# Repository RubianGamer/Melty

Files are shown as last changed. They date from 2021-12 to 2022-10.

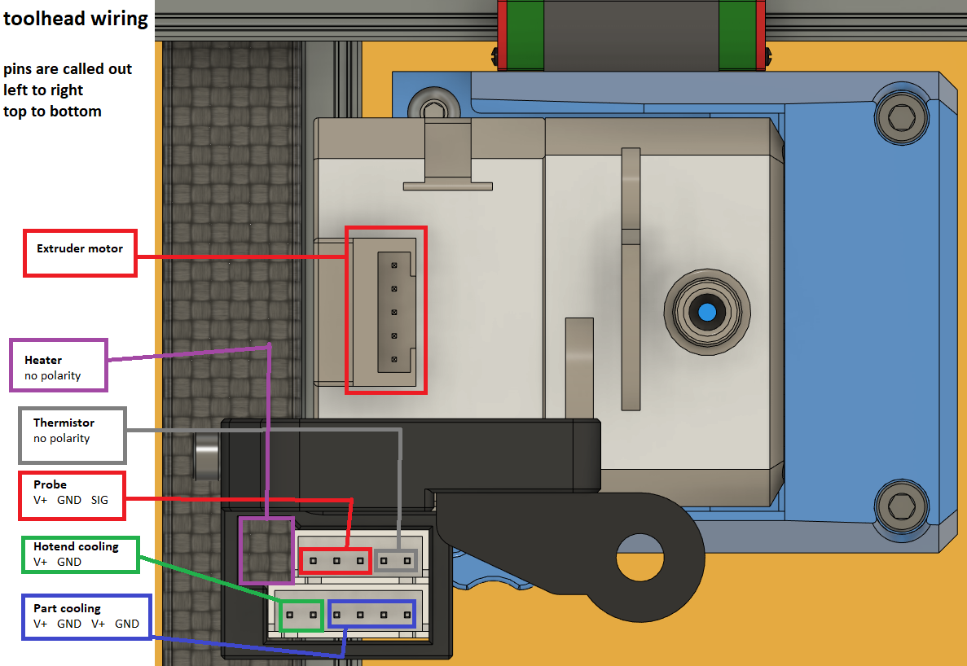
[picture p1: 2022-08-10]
beta releases/beta 3/wiring schematics/toolhead_wiring.png

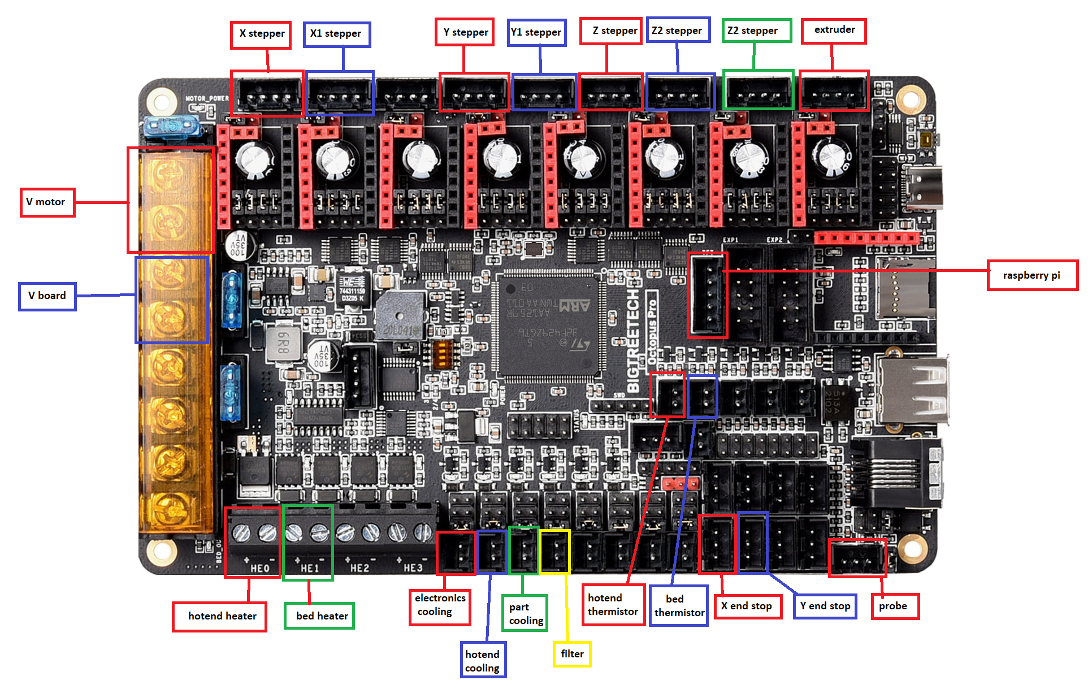
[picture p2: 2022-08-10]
beta releases/beta 3/wiring schematics/octopus wiring.png

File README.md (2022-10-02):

# Melty
 A medium to large scale, scalable crossed gantry FDM 3D printer 

# featurelist

- crossed gantry/crossXY kinematics
- fully enclosed printing chamber with air filtration
- scalable print volume of 250x250x300 to 500x500x500mm
- 3 point auto bed leveling
- options for leadscrew or belted Z
- 24v printer and 48v XY motion using 5160HV drives and BTT octopus pro
- mains powered bed
- rigid 3030 and 3060 frame extrusions
- shortest possible 12mm 2MGT belts for motion
- MGN12H rails for stationary rails, MGN9C for moving rails backed by MakerBeamXL or a carbon fiber tube
- phaetus rapido (UHF) and dragon UHF supported direct drive toolhead using a bondtech LGX (lite)
- easily accesable rear mounted electronics
- internal spool holder to reduce printer footprint and keep filament dry on long prints (external avalible for larger format spools)
- filtered air circulator to reduce smell and toxic fumes

# Discord

if you want more info on this printer, or need help with other 3d printing/printer related things, feel free to joing the discord
https://discord.gg/2XBTuWrQu5

# patreon

if you want to support my work, feel free to join my patreon
https://www.patreon.com/RubianGamer

# Renders

render_front

render_rear

render_top

irl

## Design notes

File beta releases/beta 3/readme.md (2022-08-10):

# changelog from beta 2

- added option for belted Z
- updated leadscrew driven Z for some extra Z height
- added 1515 CF tube for the gantry (not final)
- updated electronics enclosure
- added support for LGX lite extruder
- swapped to molex microfit connectors
- added support for long shaft steppers on XY
- refined motion system to handle high accel better
- magnetic panels now use larger magnets
- external spool holder for larger spool sizes
- changed nozzle brush location
- updated toolhead body for better hotend cooling
- tweaked bed frame extrusion lenghts
- better enclosed electronics
- bunch of smaller optimiziations

# planned features

- support for dragon UHF and rapido UHF
- rigid mounted side/back/bottom panels
- rubber grommets in rear panel for cable passthough (removing the connectors, they can be annoying at times)
- potentially custom extruder using bondtech BMG internals
- improved mount for XY steppers with normal sized shafts using couplers
- hinged door (yes some day this will be added :)

# removed

support for original dragon, it doesnt have enough flow to keep up (files might still be made avalible in the future)

# notes

the BOM might not be fully up to date, as stuff has been changing a lot recently and i lost track on all the changes in the BOM. it will still be a great indicator of the stuff you need for a price estimate.

render_front

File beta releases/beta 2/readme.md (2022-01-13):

changelog from beta 1:
- added a BOM that should be accurate
- added printed parts. not fully up to date, but has all the needed mechanical parts
- added sample config (untested, use with caution)
- added filtered air circulator
- added nozzle brush and purge bucket
- fixed the bed position
- added passtrough for the Z steppers
- added passthough for the reverse bowden tube
- added nameplate
- added carbon fiber gantry option
- added toolhead for rapido hotend

changes planned for next update:
- change carbon fiber gantry to 1515 tubes
- add hinging option for top and front panel
- fix T nut interferance on the makerbeam gantry
- higher part cooling fan duct
- led strips

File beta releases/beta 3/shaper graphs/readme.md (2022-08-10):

these graphs are from a 250 build with a LGX lite, leadscrew driven Z and a aluminum gantry

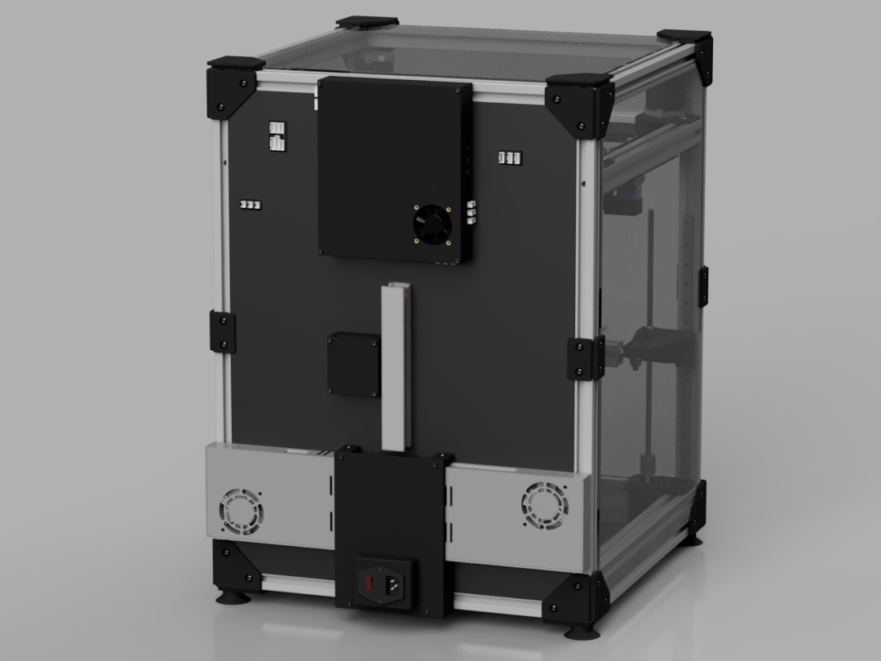
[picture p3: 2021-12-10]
beta releases/beta 1/renders/melty_electronics.png

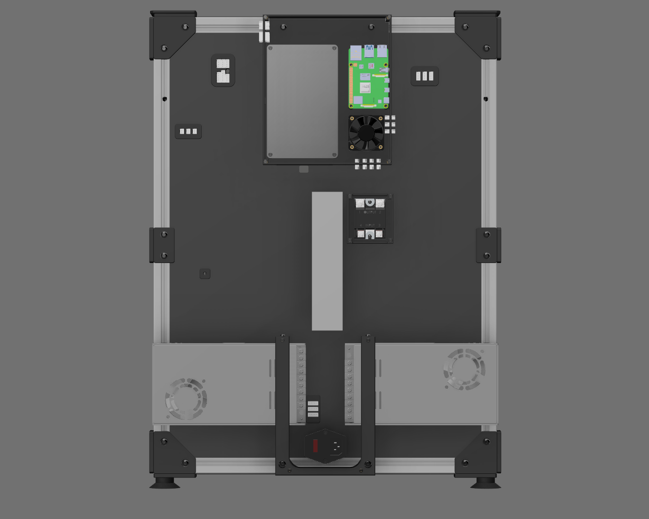
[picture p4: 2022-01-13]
beta releases/beta 2/renders/melty-electronics.png

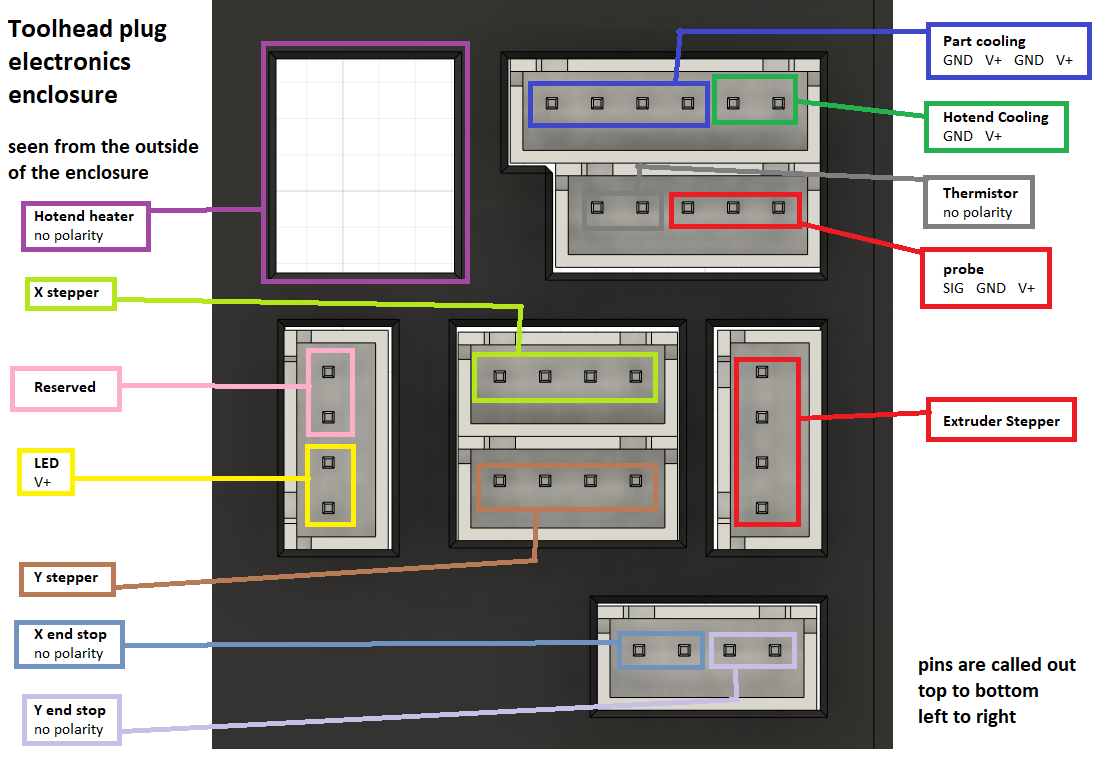
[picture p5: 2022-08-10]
beta releases/beta 3/wiring schematics/Toolhead_plug_electronics_enclosure.png

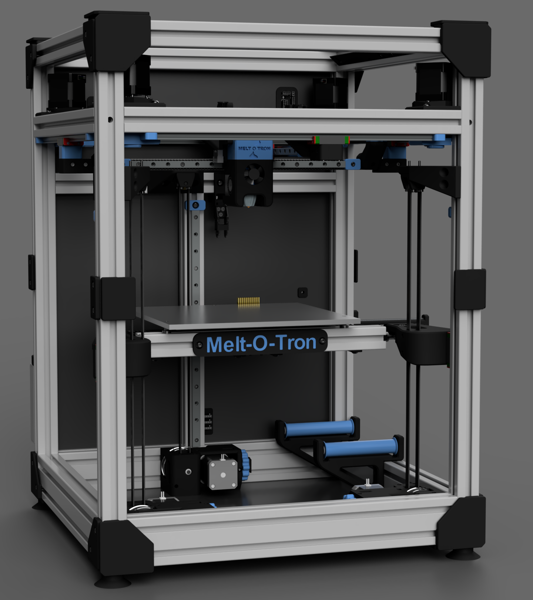
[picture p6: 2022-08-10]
beta releases/beta 3/renders/melty.png

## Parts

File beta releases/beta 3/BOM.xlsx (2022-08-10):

this part of the BOM is for the base build. You will need all of these things for every build.
some of these parts get repeated in the specific BOM for your configuration. You need to add the stuff listed under that section to this for the total quantity needed. Screws have been counted for all the possible layouts. i still recommend getting a surplus of screws for future upgrades and counting mistakes.
category | part name | quantity | obtained | source | alt source | notes
hardware | M2.5x6 BHCS | 4 |  | schrauben-expert (https://schrauben-expert.de/) | McMaster-carr (https://www.mcmaster.com/screws/) | these might be included with your hotend of choice
hardware | M2.5x8 BHCS | 4
hardware | M3x6 BHCS | 51 |  |  |  | These are exact ammounts, its recommended to get some extra
hardware | M3x8 FHCS | 15
hardware | M3x8 SHCS | 169
hardware | M3x12 BHCS | 16
hardware | M3x14 SHCS | 8
hardware | M3x20 SHCS | 27
hardware | M3x35 SHCS | 8
hardware | M5x10 BHCS | 68
hardware | M5x12 BHCS | 55
hardware | M5x25 BHCS | 4
hardware | M8x10 BHCS | 35
hardware | M8x30 BHCS | 3
hardware | M3 hex nut | 8 |  | schrauben-expert (https://schrauben-expert.de/DIN-439-Hexagon-Nut-flat-steel-plated)
hardware | M4 knurled nut | 3 |  | aliexpress (https://www.aliexpress.com/item/1005003385966630.html) |  | get them from stainless steel for better heat isolation of the bed
hardware | M3 locknut | 8 |  | aliexpress
hardware | M8 locknut | 3
hardware | M3 T-nut | 45 |  | aliexpress (https://www.aliexpress.com/item/32818082697.html) |  | roll in ones are rare, but if you can find them they will be easier to work with.
hardware | M5 T-nut | 123 |  | aliexpress (https://www.aliexpress.com/item/33023772052.html)
hardware | M3 heatset insert | 78 |  | aliexpress (https://www.aliexpress.com/item/1005002530005649.html) |  | specific size needs to be M3x5x4
hardware | 5x10x1 shim | 16 |  | schrauben-expert (https://schrauben-expert.de/DIN-125-Washer-without-bevel-A-Stainless-Steel) |  | make sure these are shims and not washers. Washers have variying heights, shims are more precise.
hardware | 6x3 magnet | 32 |  | aliexpress (https://www.aliexpress.com/item/1005001614008679.html)
hardware | 120-130mm M5 steel rod | 2 |  | aliexpress (https://www.aliexpress.com/item/1005003609354901.html) |  | used for the spool holder, if you are going with a different spool holder, you don’t need these
hardware | rubber compressor feet | 4 |  | aliexpress (https://www.aliexpress.com/item/32990144547.html) |  | if you don’t like these, any feet with a M5 hole in the bottom should work
hardware | M8 rodend | 3 |  | aliexpress (https://www.aliexpress.com/item/32741967134.html)
electronics | LRS-200-24 | 1 |  | digikey (https://www.digikey.nl/en/products/detail/LRS-200-24/1866-3332-ND/7705026?itemSeq=385607687) |  | DO NOT cheap out on the power supply, get them from a known good brand 48v is only needed if you go with 48v XY motion
electronics | LRS-200-48 | 1 |  | digikey (https://www.digikey.nl/en/products/detail/LRS-200-48/1866-3336-ND/7705025?itemSeq=385607640)
electronics | BTT octopus (pro, F446) | 1 |  | aliexpress (https://www.aliexpress.com/item/1005003349906490.html) |  | both the regular and pro will work, but you will need the pro for 48v XY motion. Non pro also needs a additional BAT85 diode as the build in probe port does not work correctly with the type of probe used
electronics | TMC2209 drivers | 4 |  | aliexpress (https://www.aliexpress.com/item/4000249242465.html) |  | you will need 4 additional drivers if you are not going with 48v XY motion
electronics | TMC5160HV drivers | 4 |  | watterott (https://shop.watterott.com/SilentStepStick-TMC5160-Stepper-motor-driver) |  | only needed when going for 48v XY motion. Make sure you get the high voltage ones, since the regular ones can only do 36v
electronics | raspberry PI 4 | 1 |  | find local source |  | PI 3B+ works as well.
electronics | wago 221-415 | 3 |  | digikey (https://www.digikey.nl/en/products/detail/221-415%2fK194-4045/2946-221-415%2fK194-4045-ND/13549349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) |  | other types of wire nuts might work as well.
electronics | fused power inlet | 1 |  | aliexpress (https://www.aliexpress.com/item/32959398453.html) |  | this one comes with a 10A fuse. I recommend replacing the fuse for something closer to the max power draw of your printer (5A for a 250 build)
electronics | JST-XH 2 pin female | 6 |  | aliexpress |  | buy one of each of the kits, they have enough for the entire build
electronics | JST-XH 3 pin female | 1
electronics | JST-XH 4 pin female | 9
electronics | JST-XH pins | 60
electronics | JST-PH 4 pin female | 8
electronics | JST-PH pins | 32
electronics | 1x2 molex male/female | 6 |  | aliexpress |  | kits come with both male and female side, and also include the needed pins for the 2x7, both links are needed as male and female plugs are sold seperately
electronics | 1x4 molex male/female | 18
electronics | 2x7 molex male/female | 3 |  | aliexpress (https://www.aliexpress.com/item/4000969264416.html) | aliexpress (https://www.aliexpress.com/item/32878728191.html)
electronics | molex pins | 150 |  | included in kits
electronics | ferrule connectors | 4 |  | aliexpress (https://www.aliexpress.com/item/33040940850.html)
electronics | thermal fuse | 1 |  | aliexpress (https://nl.aliexpress.com/item/32995866765.html) |  | get one with the max temp you are planning on using the bed at. Not recommended going above 150c, as this is the long term usage spec of the glue used on the heater
electronics | spade connectors | 20 |  | lektor (https://lecktor.com/en/connectors/291-flanged-spade-terminals-yf2-4k.html) | aliexpress (https://www.aliexpress.com/item/4000105363591.html) | make sure to get the right size for the wires you are using.
electronics | AWG16 cable | 10 meters |  | lektor (https://lecktor.com/en/cables/644-336-heluflon-fep-6y-16awg-15mm2.html) |  | motion rating is not stricly needed, but is recommended. Recommended to get 3 different colors
electronics | AWG20 cable | 10 meters |  | lektor (https://lecktor.com/en/cables/645-340-heluflon-fep-6y-20awg-05mm2.html) |  | make sure these are rated for use in drag chains. If 24AWG is out of stock, you can replace it with 20AWG.
electronics | AWG24 cable | 50 meters |  | lektor (https://lecktor.com/en/cables/646-344-heluflon-fep-6y-24awg-025mm2.html)
electronics | 3010 axial fan | 1 |  | aliexpress (https://www.aliexpress.com/item/4000608874732.html) |  | DO NOT get fans with low air flow and static pressure, you will have heat creep issues
electronics | 5010 axial fan | 1 |  | aliexpress (https://www.aliexpress.com/item/4000609105669.html) |  | get something quiet, you don’t need much cooling for the electronics.
electronics | 110-220v 20A SSR | 1 |  | ratrig (https://www.ratrig.com/hardware2/electronics/clin-ssr-40a-relay.html) |  | DO NOT cheap out and get a cheap chinese one, get one from a known good brand. Get the highest amp rated you can (within reason)
electronics | 10x11 drag chains | 2 |  | aliexpress (https://www.aliexpress.com/item/33000014666.html) |  | if you have some laying around, but don’t have end pieces, you can print these.
electronics | cable raceway | 1 |  | prited |  | easy to print, so no need to buy them seperately
motion | LDO-42STH48-2504AH(S55) or LDO-42STH48-2004MAH(ANX)(S80) | 4 |  | lukeslabonline (https://lukeslabonline.com/collections/ldo/products/longboi-ldo-nema-17-motor-high-temp-ldo-42sth48-2504ahs55) | caribou3d (https://caribou3d.com/en/annex-k3/897-09-stepper-motor-set-ldo-42sth48-2004mahanxs80.html) | these are steppers with long shafts. Normal steppers don’t have long enough shafts to work correctly. Any nema17 stepper with a shaft of at least 55mm long should work the LDO-42STH48-2504AH(S55) is great for printing at high speed, but has some issues with VFA at low printing speeds and is currently only avalible from one vendor in the USA. the LDO-42STH48-2004MAH(ANX)(S80) is a great 0.9 deg alternative, but you need to shorten the shafts a bit to not have them stick out, but have a lower top speed.
motion | 12mm 20 tooth GT2 pulley | 4 |  | aliexpress (https://www.aliexpress.com/item/33023279793.html) |  | you can swap to a 24 tooth pulley to get some more speed, but loose some acceleration. For realistic printing this doesn’t matter.
motion | 12mm GT2 belts | 5 meters |  | aliexpress (https://www.aliexpress.com/item/32952396111.html) |  | gates belts are recommended
motion | F695 bearing | 10 |  | aliexpress (https://www.aliexpress.com/item/757340601.html) |  | both ZZ and RS bearings work
motion | 695 bearing | 10 |  | aliexpress (https://www.aliexpress.com/item/558040550.html)
motion | MGN12H 350mm linear rail | 7 |  | robodigg (https://www.robotdigg.com/product/766/Quality-440C-SUS-MGN12-linear-rail-with-carriage) |  | cheap china rails will work, but its not recommended
motion | MGN9C linear rail | 2 |  | robodigg (https://www.robotdigg.com/product/779/Quality-440C-SUS-MGN9-linear-rail-with-carriage)
motion | ball bearing grease | 1 |  | source locally |  | any grease made for ball bearings should work. Don’t use oil as it doesn’t last as long
panels | top panel (440x440mm) | 1 |  | source locally |  | ideally from something transparent. Polycarbonate is recommended.
panels | side panels (600x440mm) | 3
panels | bottom panel (440x440mm) | 1 |  |  |  | ideally solid color. ACM/dibond are recommended and is easy to work with.
panels | back panel (600x440mm) | 1
buildplate | aluminum build plate | 1 |  | lektor (https://lecktor.com/en/vtd-buildplate/649-universal-250x250mm-build-plate.html) |  | make sure its cast so it doesn’t warp after repeated heating cycles. Hole mounting is the same as on the voron trident bed, so you can buy those if you have issues sourcing a bare plate.
buildplate | magnet sheet | 1 |  | lektor (https://lecktor.com/en/v2x-buildplate/481-magnetic-foil-260x260x1mm.html) |  | make sure to get a oversized magnet to make applying it easier.
buildplate | silicone heater | 1 |  | keenovo (https://keenovo.store/collections/standard-keenovo-silicone-heaters/products/keenovo-square-silicone-heater-3d-printer-build-plate-heatbed-heating-pad) |  | DO NOT get a cheap chinese heater, get a genuine one from keenovo. Recommended to have it be slightly undersized by 40mm, but some vendors might have a full cover heaters with holes cut out for the mounting.
buildplate | flexplate | 1 |  | aliexpress (https://nl.aliexpress.com/item/1005004182077447.html)
buildplate | nozzle brush | 1 |  | source locally
frame | 3030 B-Type 645mm | 4 |  | aluxprofiel | ratrig | ends do not need to be tapped
frame | 3030 B-Type 425mm (tapped) | 9 |  |  |  | both ends need to be tapped with M8 at least 10mm deep.
frame | 3030 B-Type 375mm (tapped) | 1
frame | 3030 B-Type 330mm (tapped) | 1
frame | 3030 B-Type 215mm (tapped) | 1
frame | 3060 B type 425mm (tapped) | 4
toolhead | rapido or dragon UHF | 1 |  | aliexpress (https://www.aliexpress.com/item/1005003954881267.html) | 3djake (https://www.3djake.com/phaetus/dragon-hotend-uhf) | pick whichever you like the most. rapido HF can struggle to keep up, so the UHF version is reccomended
toolhead | LGX or LGX lite | 1 |  | lektor (https://lecktor.com/en/24-extruders) |  | LGX is prefered for non speed printing, LGX lite is better for speed printing, but has lower torque output, so might struggle to keep up
toolhead | 4mm OD 3mm ID PTFE tube | 2 meters |  | aliexpress (https://www.aliexpress.com/item/1005003593762891.html) |  | get clear PTFE tube, it makes it easier to see where your filament is when loading.
toolhead | 4mm OD 1.9mm ID PTFE tube | 20cm |  | aliexpress (https://nl.aliexpress.com/item/1005001370675514.html) |  | can be anything you have laying around. Doesn’t come into contact with anything hot, so doesn’t need to be fancy tubing.
toolhead | 4010 blower | 2 |  | aliexpress (https://www.aliexpress.com/item/32798634077.html) | digikey (https://www.digikey.com/en/products/detail/delta-electronics/BFB0412HHA-A117/5022816) | delta is recommended, but might be hard to find outside of the US
toolhead | omron TL-Q5MC2 | 1 |  | lektor (https://lecktor.com/en/sensors/557-proximity-sensor-tl-q5mc2-2m-4536854114885.html) | aliexpress (https://www.aliexpress.com/item/32849513527.html?) | lektor has genuine omron switches. The aliexpress ones linked worked fine for me.
filament | ABS primary color | 2kg |  | 3djake | 3djake | 3djake niceABS is rebranded titanX, and prints very easily on non enclosed printers. Filamentum can also be printed without enclosure, but might encounter some warping on larger parts you can also print the parts out of PC for increased thermal resistance.
filament | ABS secundary color | 500g
filter | 5015 blower | 2 |  | aliexpress (https://www.aliexpress.com/item/1005003652882829.html) |  | get cheap fans with ball bearings, they will be used in a really hot enviroment so wont have the longest lifetime. Recommended to get some spares
filter | activated carbon | 1 liter |  | source locally |  | DO NOT get acid washed carbon, this can cause your printer to rust really fast. You want to get (virgin) coconut shell based carbon that is steam activated
aluminum gantry
gantry | 1515 (makerbeam XL) extrusion 470mm | 2 |  | makerbeam (https://www.makerbeam.com/makerbeamxl/makerbeamxl-15x15mm-profile-lengths-anodised-in-bl/) |  | other types of 1515 extrusions will work as well, just make sure to get the right T-nuts for them. Ends don’t need to be tapped
gantry | M3 makerbeam XL T-nut | 38 |  | makerbeam (https://www.makerbeam.com/t-slot-nuts-for-makerbeamxl-50p.html) |  | you can also use M3 hex nuts with printed traps.
carbon fiber gantry
gantry | 15x15x13 cf tube 470mm long | 2 |  | source locally | contact mellow | mellow makes custom carbon fiber tubes at a little cost. All the files needed for it are in the repo. If you can get them from mellow, it is highly recommended as cutting/drilling carbon fiber can be a pain to do correctly.
gantry | M3 washer | 10 |  | schrauben-expert (https://schrauben-expert.de/DIN-9021-Washer-large-Stainless-Steel)
gantry | M3 locknut | 10 |  | aliexpress (https://www.aliexpress.com/item/32798773566.html) |  | can be normal hex nuts, but nylock nuts are recommended since you cant torque them a lot without crushing the carbon fiber tube.
gantry | M3 heatset insert | 28 |  | aliexpress (https://www.aliexpress.com/item/1005002530005649.html)
leadscrew driven Z
recommended for larger build volumes
Z axis | 335-370mm leadscrew | 3 |  | aliexpress (https://www.aliexpress.com/item/32792571155.html) |  | recommended is 2mm pitch, 8mm lead, but finer will work as well. Finer leadscrews are recommeded for larger build volumes to aid in keeping the bed up on power down make sure you match the leadscrew nut lead/pitch to the leadscrews you are getting
Z axis | leadscrew nut | 3 |  | aliexpress (https://www.aliexpress.com/item/32696626893.html)
Z axis | flexible coupler | 3 |  | aliexpress (https://www.aliexpress.com/item/4000811647280.html) | aliexpress (https://www.aliexpress.com/item/32862693235.html) | alternate source is a different type of flexible coupler. Supposed to work better then other types of flexible couplers, but not personally tested it.
Z axis | 40mm stepper motor | 3 |  | ratrig (https://www.ratrig.com/hardware2/electronics/nema-17-stepper-motor.html) |  | max supported length is 48mm, but 40mm should be plenty
Z axis | 5mm ball bearing | 3 |  | aliexpress (https://www.aliexpress.com/item/1005003281616396.html) |  | used to support the couper so it doesn’t compress under the weight of the bed, but still allowing the coupler to flex.
Z axis | M3 locknut | 12 |  | aliexpress (https://www.aliexpress.com/item/32798773566.html)
belt driven Z
not recommended for larger build volumes as you might run into issues with the bed falling down when the motors get powered down
Z axis | 60mm stepper motor | 3 |  | OMC-stepperonline (https://www.omc-stepperonline.com/3-pcs-nema-17-bipolar-1-8deg-65ncm-92oz-in-2-1a-3-36v-42x42x60mm-4-wires-3-17hs24-2104s) |  | larger stepper motors are recommended over smaller ones for the increased detent torque
Z axis | GT2 80T 9/10mm pulley | 3 |  | aliexpress (https://nl.aliexpress.com/item/32997318588.html) |  | if you want to save some money, you should be able to print these as well, models can be found online.
Z axis | GT2 20T 9/10mm pulley | 3 |  | aliexpress (https://nl.aliexpress.com/item/32995102911.html) |  | can be replaced with 16T pulleys.
Z axis | GT2 16T 9/10mm pulley | 3 |  | aliexpress (https://nl.aliexpress.com/item/32995138803.html)
Z axis | GT2 20T 9/10mm idler | 3 |  | aliexpress (https://nl.aliexpress.com/item/32750484488.html) |  | can be both smooth and toothed.
Z axis | 9/10mm 202-GT2 closed loop belt | 3 |  | aliexpress (https://nl.aliexpress.com/item/4000034021834.html) |  | belt length needs to be 202mm
Z axis | 2GT 9/10mm open loop belt | 3 meters |  | aliexpress (https://nl.aliexpress.com/item/32608096392.html)
Z axis | 695 bearing | 9 |  | aliexpress (https://www.aliexpress.com/item/558040550.html) |  | both ZZ and RS bearings will work
Z axis | M3 heatset insert | 21 |  | aliexpress (https://www.aliexpress.com/item/1005002530005649.html)
Z axis | M3 locknut | 6 |  | aliexpress (https://www.aliexpress.com/item/32798773566.html) |  | normal M3 hex nuts will work as well, but you might loose belt tension over time due to vibrations
Z axis | M5x60 D cut shaft | 3 |  | aliexpress (https://nl.aliexpress.com/item/4000303705414.html) |  | make sure it’s a D shaft
Z axis | M5x25 shaft | 3 |  | aliexpress (https://www.aliexpress.com/item/4000473863693.html) |  | make sure it’s a round shaft, D shafts can cause damage to the bearings inside the idlers

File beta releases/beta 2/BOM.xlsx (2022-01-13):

category | part name | quantity | obtained | source | notes
hardware | M2.5x6 SHCS | 4 |  | schrauben-expert (https://schrauben-expert.de/) | get whichever type of material you want. Numbers given are higher then actually used to account for counting errors. Exact ammounts are given for M5x25 and M8x30 M3x6SHCS only needed for carbon fiber gantry M2,5x8 SHCS should be included with your hotend of choice
hardware | M2.5x8 SHCS | 4
hardware | M3x6 BHCS | 25
hardware | M3x6 SHCS | 10
hardware | M3x8 FHCS | 15
hardware | M3x8 SHCS | 150
hardware | M3x12 BHCS | 2
hardware | M3X12 SHCS | 25
hardware | M3x14 SHCS | 15
hardware | M3x20 SHCS | 50
hardware | M3x35 SHCS | 20
hardware | M4x14 BHCS | 6
hardware | M5X10 BHCS | 90
hardware | M5x12 BHCS | 30
hardware | M5X25 BHCS | 5
hardware | M8x10 BHCS | 40
hardware | M8x30 BHCS | 3
hardware | M3 nut | 10
hardware | M4 knurled nut | 3 |  | aliexpress (https://www.aliexpress.com/item/1005003385966630.html)
hardware | M3 locknut | 25 |  | aliexpress (https://www.aliexpress.com/item/32798773566.html)
hardware | M8 locknut | 5
hardware | M3 T nut | 65 |  | aliexpress (https://www.aliexpress.com/item/32818082697.html) | can be any type, but roll in nuts are prefered, since you can insert them after building the frame. Needs to be compatible with 3030 B type extrusions. Links have both M3 and M5 as options
hardware | M5 T nut | 150 |  | rat rig (https://www.ratrig.com/aluminium-profiles/t-slot-30-b-type/accessories-30-series/nuts/t-nut-square-3030-1-unit.html)
hardware | makerbeamXL M3 nut | 50 |  | makerbeam (https://www.makerbeam.com/t-slot-nuts-for-makerbeamxl-50p.html) | not needed if you are going with a carbon fiber gantry.
hardware | M3 heatset insert | 85 |  | lektor (https://lecktor.com/en/nuts/506-230-threaded-insert-m3x5x4.html) | get the M3 x D5.0 x L4.0 variant
hardware | M3x0.5 washer | 10 |  | schrauben-expert (https://schrauben-expert.de/DIN-125-Washer-without-bevel-A-32x7x05-Steel-zinc-plated) | only needed when using the carbon fiber gantries, alternatively, you can get the larger ones for more even weight distribution https://schrauben-expert.de/DIN-9021-Washer-large-32x9x08-Steel-zinc-plated
hardware | 5x10x1 shim | 20 |  | schrauben-expert (https://schrauben-expert.de/DIN-125-Washer-without-bevel-A-53x10x10-Brass) | material can also be stainless steel
hardware | 5mm ball bearing | 3 |  | aliexpress (https://www.aliexpress.com/item/1005003281616396.html) | used to take the load off of the flexible couplings while still allowing them to flex
hardware | 6x3 neodynium magnet | 60 |  | alexpress (https://www.aliexpress.com/item/1005001614008679.html) | other types of magnets of the same size might work as well, but will be less strong
hardware | 120-125mm M5 steel rod | 2 |  | aliexpress (https://www.aliexpress.com/item/1005003609354901.html) | used for the spool holder. If you are using a different spool holder you can ignore these
hardware | rubber compressor feet | 4 |  | aliexpress (https://www.aliexpress.com/item/32990144547.html)
hardware | M8 rodend | 3 |  | aliexpress (https://www.aliexpress.com/item/32741967134.html)
electroncis | LRS-200-24 | 1 |  | digikey (https://www.digikey.nl/en/products/detail/LRS-200-24/1866-3332-ND/7705026?itemSeq=385607687) | DO NOT cheap out on the power supply
electroncis | LRS-200-48 | 1 |  | digikey (https://www.digikey.nl/en/products/detail/LRS-200-48/1866-3336-ND/7705025?itemSeq=385607640) | only needed if you are running 48V for XY motion, DO NOT cheap out
electroncis | BTT octopus PRO | 1 |  | aliexpress (https://www.aliexpress.com/item/1005003349906490.html) | non pro board will work if you are not running 48V for XY motion
electroncis | BTT TMC2209 driver | 4 |  | aliexpress (https://www.aliexpress.com/item/4000249242465.html) | need 4 additional ones if you are not running 48V for XY motion
electroncis | BTT TMC52160 PRO driver | 4 |  | aliexpress (https://www.aliexpress.com/item/1005003353124990.html) | only needed if you are running 48V XY motion, make sure to get the pro version. The regular ones are not able to handle 48V
electroncis | raspberry pi 4 | 1 |  | sossolutions (https://www.sossolutions.nl/raspberry-pi-4-model-b-4gb) | the pi 3B can work as well. pi zero 2 w will work as well (has the same CPU as the 3B), but has limited IO and is not recommended
electroncis | wago 221-415 | 3 |  | digikey (https://www.digikey.nl/en/products/detail/221-415%2fK194-4045/2946-221-415%2fK194-4045-ND/13549349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)
electroncis | fused power inlet | 1 |  | aliexpress (https://www.aliexpress.com/item/32959398453.html)
electroncis | JST-XH 2 pin male | 8 |  | aliexpress (https://www.aliexpress.com/item/1005003444647111.html) | can be bought seperately or as a kit. Get the 2.54mm option in the supplied link 2 times
electroncis | JST-XH 2 pin female | 8
electroncis | JST-XH 4 pin male | 20
electroncis | JST-XH 4 pin female | 20
electroncis | JST-XH 5 pin male | 6
electroncis | JST-XH 5 pin female | 6
electroncis | JST-XH 6 pin male | 6
electroncis | JST-XH 6 pin female | 6
electroncis | JST-XH pins | 170
electroncis | JST-PH 4 pin female | 8 |  |  | can be bought seperately or as a kit. Buy the 2mm option
electroncis | JST-PH pins | 60
electroncis | molex microfit 3 connector | 1 |  | aliexpress (https://www.aliexpress.com/item/1005002970259261.html) | this is a kit that has all the connectors and pins needed. If buying seperatley, you need at least 4 pins, a male and female body.
electroncis | ferrule connectors | 1 |  | aliexpress (https://www.aliexpress.com/item/4001147539879.html) | has both a crimping tool and all the crimps you need
electroncis | thermal fuse | 1 |  | lektor (https://lecktor.com/en/v2x-electronics/441-190-termal-fuse.html) | get one with apropriate temp for your usecase. For general usecase around 130c is recommended
electroncis | spade connectors | 20 |  | digikey (https://www.digikey.nl/en/products/detail/te-connectivity-amp-connectors/2-520181-2/289246) | make sure to get ones sized for 18 or 16AWG wires
electroncis | Insulated Crimp Receptical | 6 |  | digikey (https://www.digikey.nl/en/products/detail/te-connectivity-amp-connectors/170604-1/5157069) | make sure to get ones sized for 18 or 16AWG wires. Ones linked are for AWG16 cables
electroncis | AWG16 cable | 4 meters |  | lektor (https://lecktor.com/en/cables-connectors/307-black-wire-h07v-k-16awg.html) | any insulation will do since these wires are stationary. Recommend getting a meter of black and red, and 2 meters of green (or whatever color coding used in your region
electroncis | AWG20 cable | 5 meters |  | lektor (https://lecktor.com/en/cables-connectors/645-340-heluflon-fep-6y-20awg-05mm2.html) | needs to have PTFE or silicone insulation, or anything rated for use in drag chains. Used for power for the heater. Get in any color you want.
electroncis | AWG 24 cable | 30 meters |  | lektor (https://lecktor.com/en/cables-connectors/646-344-heluflon-fep-6y-24awg-025mm2.html) | needs to have PTFE or silicone insulation, or anything rated for use in drag chains. Recommend getting black, red and a different color to keep positive, negative and signal easily identifiable so you don’t end up sending 24v down a signal line
electroncis | D2F-5L switch | 2 |  | lektor (https://lecktor.com/en/sensors/438-spdt-switch-d2f-5l.html)
electroncis | bat85 diode | 1 |  | lektor (https://lecktor.com/en/sensors/359-bat85-diode.html) | get from trusted source, if its not as advertized, you might blow up your control board. The octopus has a dedicated sense port, but they seem to be a toss up if they work correctly.
electroncis | omron TL-Q5MC2 2M | 1 |  | lektor (https://lecktor.com/en/v2x-electronics/557-proximity-sensor-tl-q5mc2-2m.html) | B stock from aliexpress will work, but they are less accurate, but generally are accurate enough for our usecase
electroncis | 3010 axial fan | 1 |  | aliexpress (https://www.aliexpress.com/item/4000608874732.html) | DO NOT get ones with low static pressure and CFM, you might get heat creep issues if you do. Higher is better
electroncis | 4010 radial fan | 2 |  | aliexpress (https://www.aliexpress.com/item/32798634077.html) | get the 24v dual ball variant. If you need more part cooling, look for fans with higher CFM
electroncis | 5010 axial fan | 1 |  | aliexpress (https://www.aliexpress.com/item/4000609105669.html)
electroncis | 110/220V 20A SSR | 1 |  | rat rig (https://www.ratrig.com/hardware2/electronics/clin-ssr-40a-relay.html) | DO NOT get these from aliexpress, get them from a known brand name. higher current rating is prefered
electroncis | 10x11 drag chains | 2 |  | aliexpress (https://www.aliexpress.com/item/33000014666.html) | can buy less and use printed end pieces. Still need around 80cm for a 250 build
electroncis | cable raceway | 1 |  | printed | you don’t have to buy these, there are 3d printed alternatives.
motion | LDO-42STH47-2504AC | 4 |  | rat rig (https://www.ratrig.com/hardware2/electronics/nema-17-stepper-motor.html) | other motors might work, but these are the fastest avalible. Max supported body length is 60mm
motion | LDO-42STH40-1684AC | 3 |  |  | pretty much all steppers with decent torque will work here. Max supported body length is 48mm
motion | 12mm 2GT belts | 5 meters |  | aliexpress (https://www.aliexpress.com/item/32952396111.html) | recommend gates belts, but other brands might work as well. Larger build volumes will need to have longer belts.
motion | 20 tooth 13mm 2GT pulley | 4 |  | aliexpress (https://www.aliexpress.com/item/33023279793.html) | make sure to get them with a 5mm bore, or match the size of the shaft of your stepper if you are using different steppers. Larger pulleys can result in higher possible speed, but less accuracy. Up to 25T 2GT is supported
motion | F695 bearing | 8 |  | aliexpress (https://www.aliexpress.com/item/757340601.html) | either RS or ZZ will work
motion | 695 bearing | 6 |  | aliexpress (https://www.aliexpress.com/item/558040550.html) | either RS or ZZ will work
motion | MGN12H 350mm | 7 |  | aliexpress (https://www.aliexpress.com/item/32829826159.html) | 3 are for Z, 4 are for XY. If you are building a different size, get appropraitely sized rails. China rails are good enough for our usecase. Hiwin rails are massive overkill
motion | MGN9C 300mm | 2 |  | aliexpress (https://www.aliexpress.com/item/32773296501.html) | china rails are good enough for our usecase, hiwin rails are massive overkill
motion | 335mm leadscrew | 3 |  | aliexpress (https://www.aliexpress.com/item/32792571155.html) | pitch 2mm lead 8mm is recommended. Finer will give more resolution, but is not strictly needed. You should be able to use a stepper with integrated leadscrew of 360mm if you do not like using couplers, but this is untested and might not work
motion | leadscrew nut | 3 |  | aliexpress (https://www.aliexpress.com/item/32696626893.html) | make sure to match the pitch and lead of the leadscrews you get
motion | flexible coupler | 3 |  | aliexpress (https://www.aliexpress.com/item/4000811647280.html) | get with a 5mm and 8mm bore. Other types might work as well.
panels | top panel | 1 |  | flexinplex (https://www.flexinplex.nl/home) | size of the panel is 440x440 mm. clear polycarbonate is prefered. other materials can work as well
panels | bottom panel | 1 |  |  | size of the panel is 440x440 mm. opague panel is prefered (ACM/dibond work well)
panels | rear panel | 1 |  |  | size of panel is 600x440 mm. opague panel is prefered (ACM/dibond work well).
panels | side/front panel | 3 |  |  | size of panel is 600x440 mm. clear polycarbonate is prefered. Other materials can work as well. If you are using hinged doors, get 600x220 mm 2 times
buildplate | aluminium build plate | 1 |  | lektor (https://lecktor.com/en/v18-buildplate/649-universal-250x250mm-build-plate.html) | get one at least 8mm thick. Make sure its cast so it does not warp when heated up. Mounting is the same as the voron beds, so if its easier to source a voron bed, you can get those.
buildplate | magnet sheet | 1 |  | lektor (https://lecktor.com/en/v2x-buildplate/481-magnetic-foil-260x260x1mm.html) | get a slightly oversized sheet so you can trim it after applying
buildplate | silicone heater pad | 1 |  | keenovo (https://keenovo.store/collections/standard-keenovo-silicone-heaters/products/keenovo-square-silicone-heater-3d-printer-build-plate-heatbed-heating-pad) | you want one that is undersized from the aluminum plate by about 20mm. The heater mat includes a thermistor, so no need to buy one for the bed.
buildplate | buildplate | 1 |  | aliexpress (https://www.aliexpress.com/item/1005003319211748.html) | get with whatever surface you prefer. Make sure it’s the same size as the bed, as a larger plate will interfere with the nozzle brush.
frame | 3030 extrusion 645mm long | 4 |  | rat rig (https://www.ratrig.com/aluminium-profiles/t-slot-30-b-type/t-slot-3030-b.html) | B-type T slot
frame | 3030 extrusion 425mm long | 9 |  |  | B-type T slot. ends need to be tapped with M8
frame | 3060 extrusion 425mm long | 4 |  |  | B-type T slot. ends need to be tapped with M8
frame | 3030 extrusion 335mm long | 1 |  |  | B-type T slot. ends need to be tapped with M8
frame | 3030 extrusion 340mm long | 1 |  |  | B-type T slot. ends need to be tapped with M8
frame | 3030 extrusion 220mm long | 1 |  |  | B-type T slot. ends need to be tapped with M8
gantry | makerbeamXL 470mm long | 2 |  | makerbeam (https://www.makerbeam.com/makerbeamxl/makerbeamxl-15x15mm-profile-lengths-anodised-in-bl/) | not needed when using carbon fiber tubes for the gantry
gantry | 13x13x10 CF tube 470mm long | 2 |  | carbonwinkel (https://www.carbonwinkel.nl/carbon-plaat-staaf-buis-materiaal/carbon-buis-vierkant-gepultrudeerd-vinylester-carbon) | not needed when using the makerbeamXL for the gantry
toolhead | LGX extruder | 1 |  | lektor (https://lecktor.com/en/extruders/729-lgx-large-gears-extruder.html) | currently the only supported extruder
toolhead | dragon or rapido | 1 |  | aliexpress (https://nl.aliexpress.com/item/1005003456746319.html) | rapido is recommended, since the dragon might not be able to keep up with high speed printing very well. When going with the rapido, its up to you if you want the UHF, the fan duct is designed for the HF variant, so cooling wont be optimal
toolhead | 4mm OD 1,9mm ID PTFE tube | 10cm |  | aliexpress (https://www.aliexpress.com/item/1005001370675514.html) | can be anything you have laying around. Doesn’t need to be fancy since it wont come into contact with the nozzle
toolhead | 4mm OD 3 mmID PTFE tube | 2 meters |  | aliexpress (https://www.aliexpress.com/item/1005003593762891.html) | recommend using a (semi) clear tube so you can see where the filament is when loading/unloading
filament | ABS/ASA, primary color | 1kg |  |  | get whichever color you like. Black is recommended
filament | abs/ASA, secundary color | 250g |  |  | pick whichever color you fancy
filament | PLA/PETG | 1kg |  |  | used for the electronics and panel clips. If you are printing the electronics stuff in ABS, add 500g ABS and remove 600g PLA. If you are printing the panel mounts out of ABS, remove 500g PLA and add 450g ABS.
filter | 5015 blower | 2 |  |  | get ones with as high static pressure with decent flow as possible that are not expensive. They are not expected to last very long since they are positioned right under the bed so work in a enviroment they are not rated for.
filter | activated carbon | 1kg |  |  | DO NOT buy acid washed carbon, these might cause your printer to rust really quickly. Get steam activated, coconut based carbon in pallet shape sized around 4x8mm.
misc | nozzle brush | 1 |  | aliexpress (https://www.aliexpress.com/item/1005002042961868.html) | any generic nozzle brush will work.
note for sourcing links: currently they are what I personally bought, and thus are focused towards a EU/netherlands shipping adress. Other sources might follow later for more general EU/US/asia sourcing

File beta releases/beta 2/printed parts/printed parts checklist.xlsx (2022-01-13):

 | printed part name | remarks | needed | printed
electronics | electronics enclosure | can be printed out of PLA | 1
 | electronics lid | can be printed out of PLA | 1
 | end stop inlet |  | 1
 | PSU mount cover | can be printed out of PLA | 1
 | PSU mount bracket | can be printed out of PLA | 1
 | SSR cover | can be printed out of PLA | 1
 | SSR enclosure | can be printed out of PLA | 1
 | stepper inlet |  | 1
 | toolhead inlet |  | 1
motion | bed rail mount front left |  | 1
 | bed rail mount front right |  | 1
 | bed rail mount rear |  | 1
 | belt clamp left | print in accent color | 2
 | belt clamp lid | print in accent color | 4
 | belt clamp right | accent color | 2
 | belt tensioner | 100% infill | 4
 | end stop mount |  | 1
 | gantry belt spacer left |  | 1
 | gantry belt spacer right |  | 1
 | gantry belt bracket left |  | 2
 | gantry belt bracket right |  | 2
 | gantry mount spacer | print in accent color | 2
 | motor mount bottom | print in accent color | 4
 | motor mount top |  | 4
 | X gantry mount |  | 2
 | Y gantry mount |  | 2
 | Z axis drag chain mount bed |  | 1
 | Z axis drag chain mount frame |  | 1
 | Z axis drag chain mount bed |  | 1
 | Z axis motor mount front |  | 2
 | Z axis motor mount rear |  | 1
CF gantry | belt bracket mount CF tube | only needed for CF gantry | 4
 | CF tube mounting | only needed for CF gantry | 4
 | gantry belt bracket left CF tube | only needed for CF gantry | 2
 | gantry belt bracket right CF tube | only needed for CF gantry | 2
 | X gantry mount CF tube | only needed for CF gantry | 2
 | Y gantry mount CF tube | only needed for CF gantry | 2
panels | bottom panel mount | can be printed in PLA | 4
 | corner panel magnet holder frame | can be printed in PLA | 8
 | corner panel magnet holder panel | can be printed in PLA | 8
 | corner panel mounts | can be printed in PLA | 12
 | front panel magnet holder frame | can be printed in PLA | 2
 | front panel magnet holder panel | can be printed in PLA | 2
 | side panel mounts | can be printed in PLA | 6
toolhead | toolhead bottom | either dragon or rapido | 1
 | toolhead backplate | either dragon or rapido, 100% infill | 1
 | toolhead top | either dragon or rapido | 1
 | drag chain mount toolhead |  | 1
 | drag chain mount frame |  | 1
misc | bed corner bracket | optional part | 2
 | nameplate | decoration purpuse | 1
 | nameplate text | decoration, print in accent | 1
 | spool holder frame |  | 2
 | spool holder spinny part | print in accent | 2

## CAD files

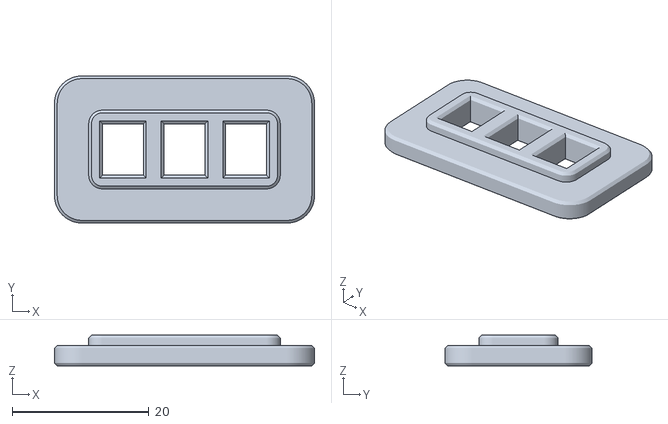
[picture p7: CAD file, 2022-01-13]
beta releases/beta 2/printed parts/electronics/end stop inlet 2X.stl
38.0 x 21.5 x 4.50

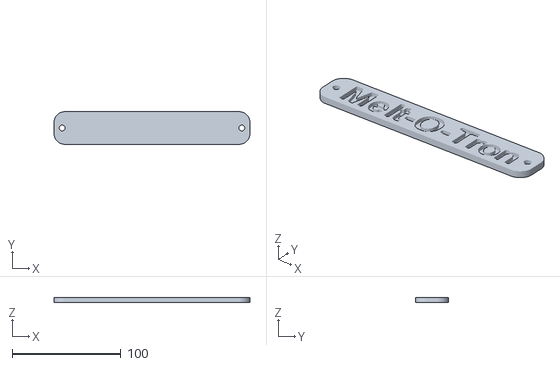
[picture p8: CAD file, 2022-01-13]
beta releases/beta 2/printed parts/misc/nameplate.stl
180.0 x 30.0 x 5.00

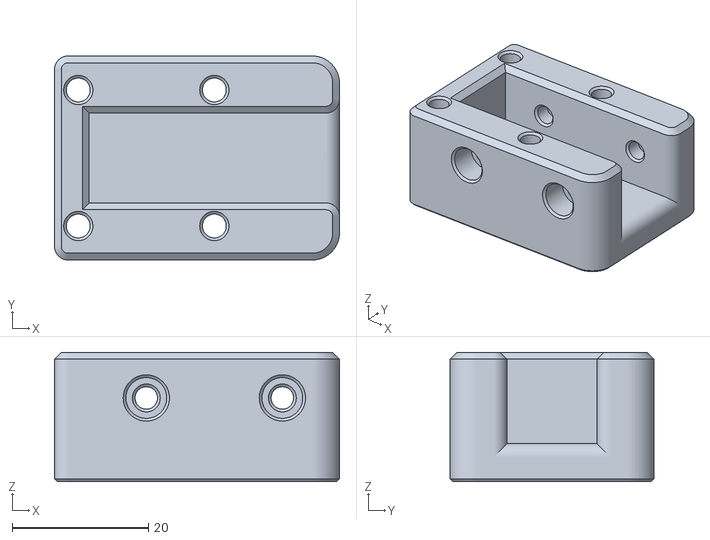
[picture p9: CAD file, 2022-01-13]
beta releases/beta 2/printed parts/motion/CF gantry/Y gantry mount CF tube 2X.stl
41.9 x 30.0 x 19.0

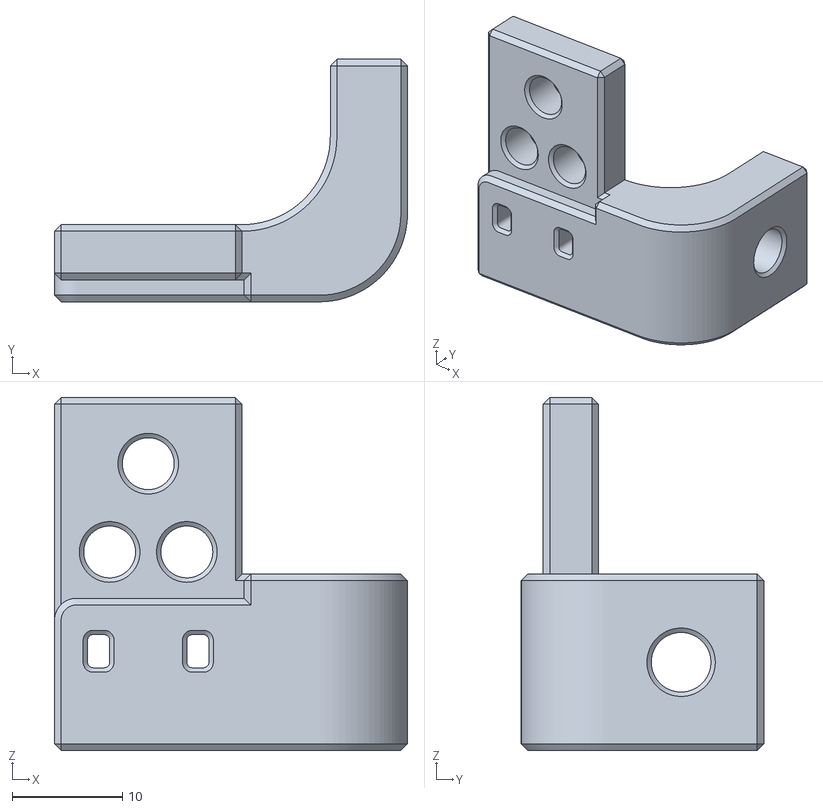
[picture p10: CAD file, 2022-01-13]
beta releases/beta 2/printed parts/motion/Z axis drag chain mount bed.stl
32.0 x 22.0 x 32.0

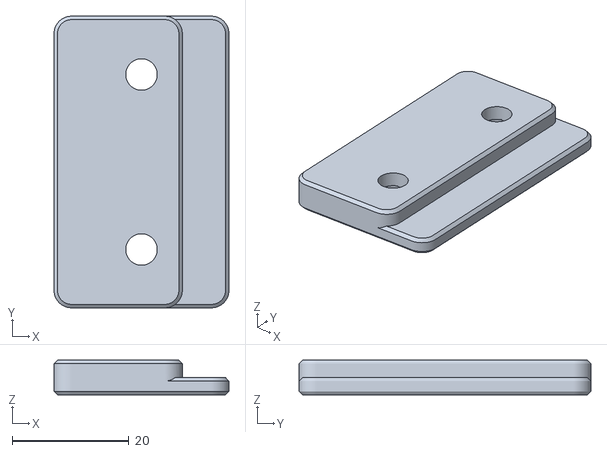
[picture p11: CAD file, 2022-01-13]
beta releases/beta 2/printed parts/panels/side panel mounts 6X.stl
30.0 x 50.0 x 6.00

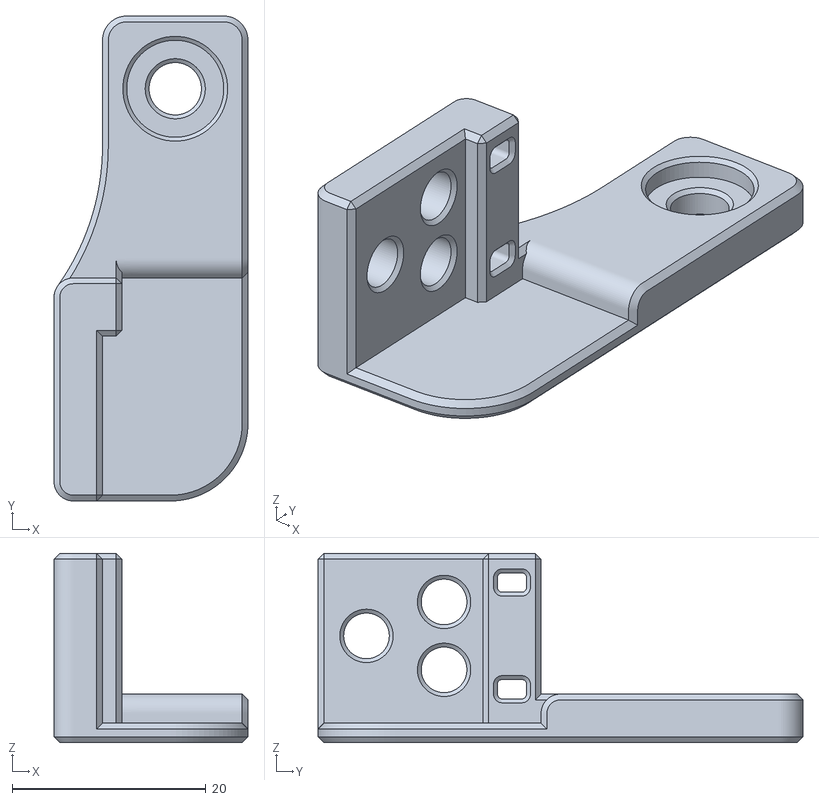
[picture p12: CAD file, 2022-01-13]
beta releases/beta 2/printed parts/toolhead/drag chain mount frame.stl
20.0 x 50.0 x 19.5

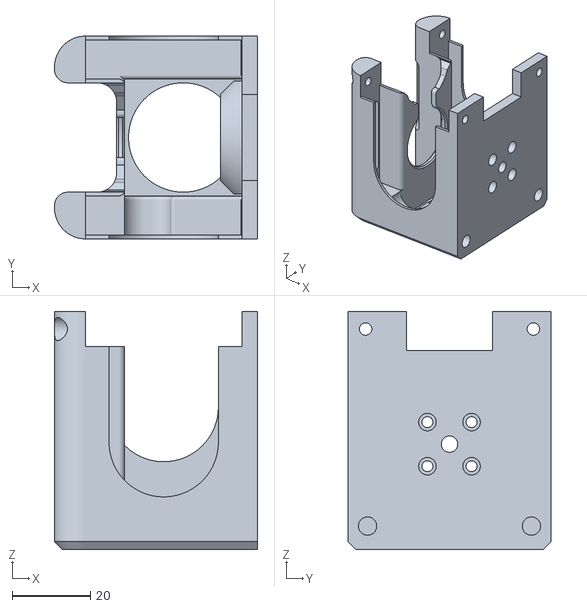
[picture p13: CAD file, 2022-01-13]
beta releases/beta 2/printed parts/toolhead/dragon/toolhead bottom.stl
52.1 x 52.0 x 61.0

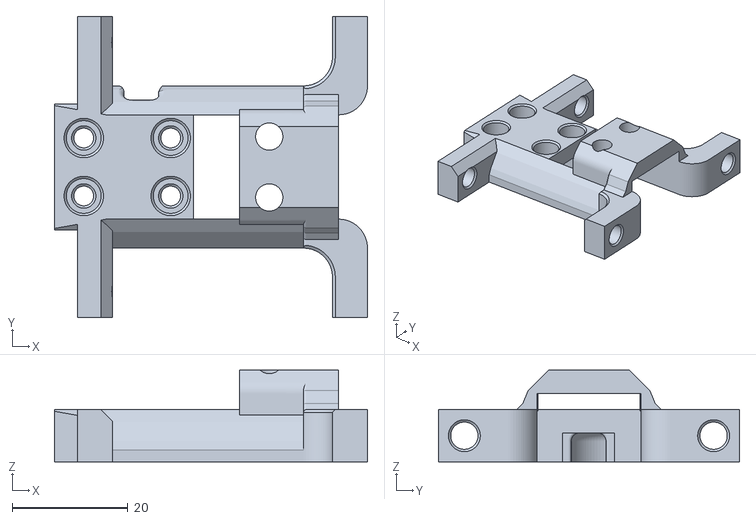
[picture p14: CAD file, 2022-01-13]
beta releases/beta 2/printed parts/toolhead/phaetus rapido/toolhead backplate (100% infill).stl
54.0 x 52.0 x 15.8

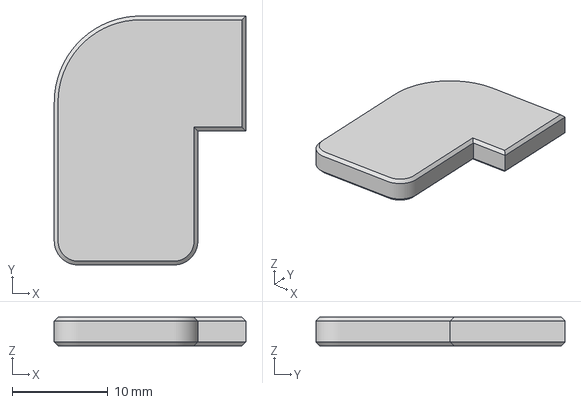
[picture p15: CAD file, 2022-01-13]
beta releases/beta 2/printed parts/tools/pulley alignment tool.3mf
20.0 x 26.0 x 3.00 mm

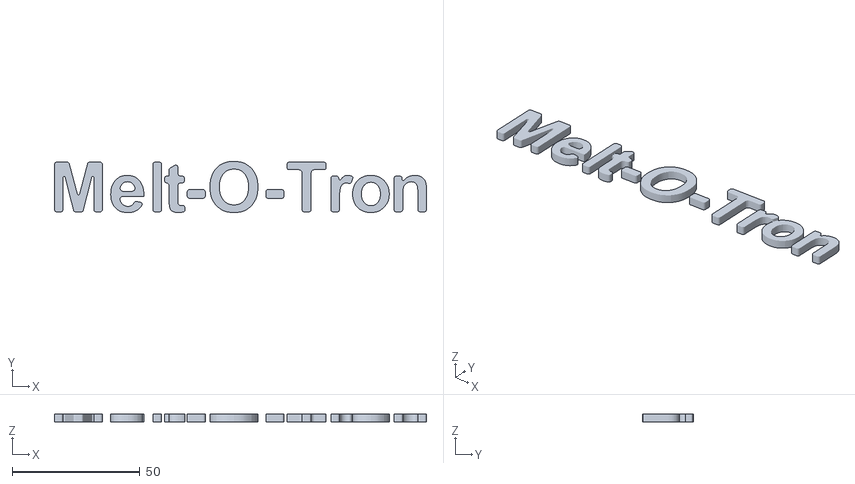
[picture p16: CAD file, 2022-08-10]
beta releases/beta 3/printed parts/bed/text.stl
145.7 x 20.1 x 3.00

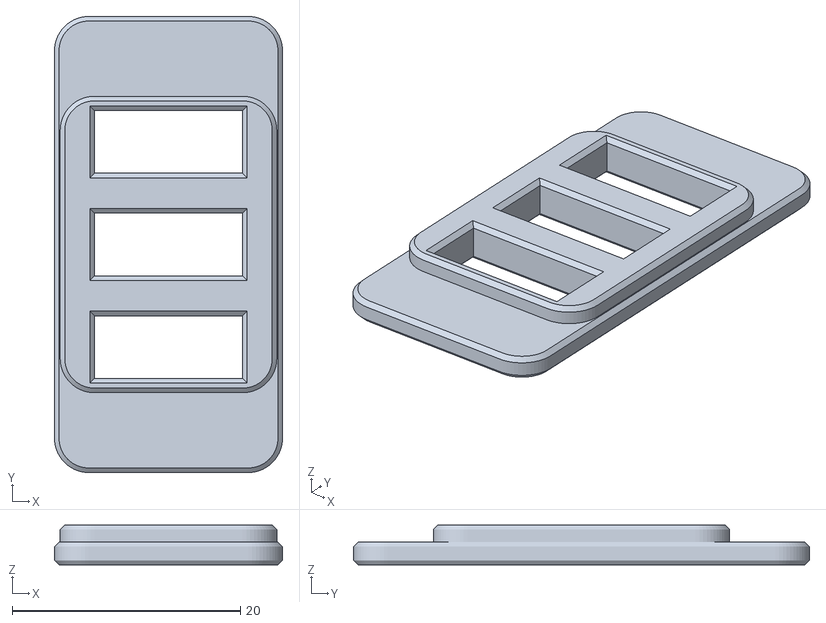
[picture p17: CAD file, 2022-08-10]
beta releases/beta 3/printed parts/electronics/Z stepper inlet.stl
20.0 x 40.0 x 3.50

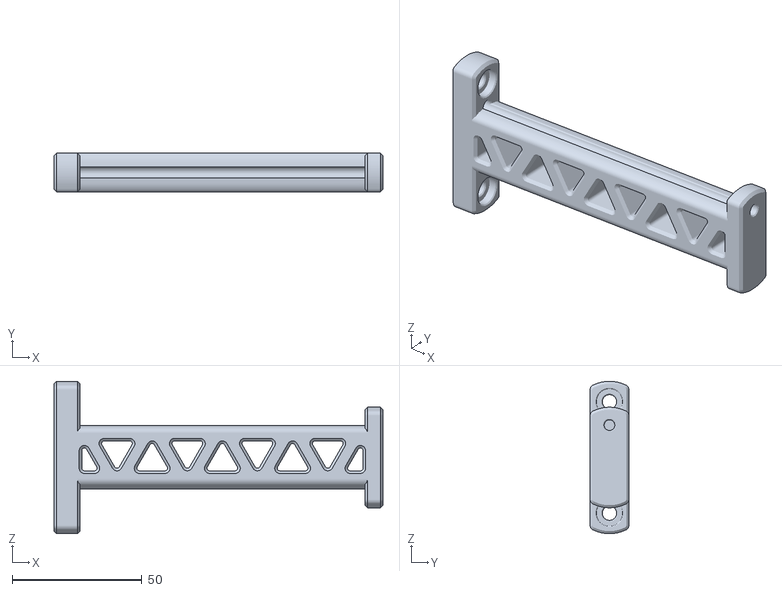
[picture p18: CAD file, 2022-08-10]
beta releases/beta 3/printed parts/misc/external spool holder.stl
127.0 x 15.0 x 58.8

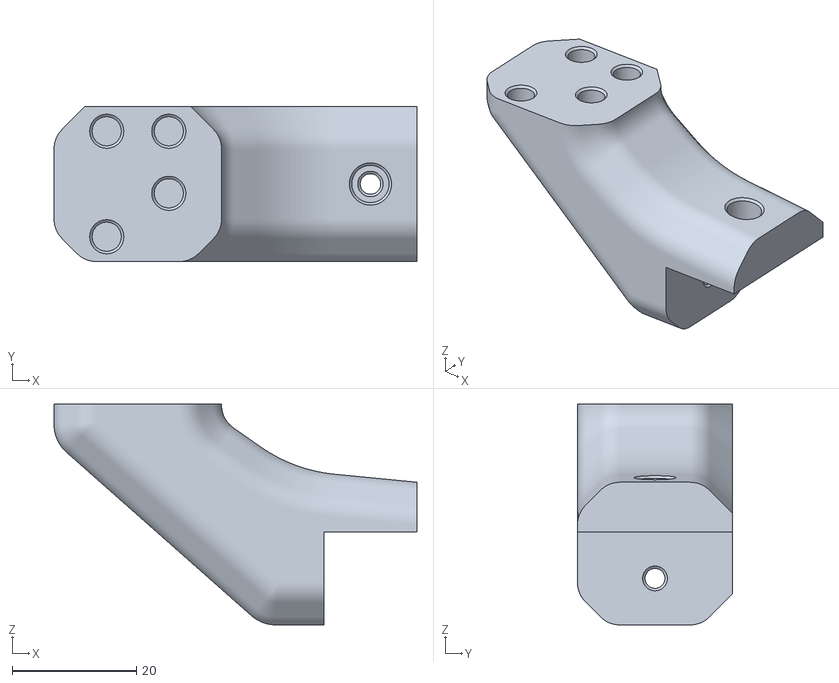
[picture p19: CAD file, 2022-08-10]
beta releases/beta 3/printed parts/motion/belt bracket left X.stl
58.5 x 25.0 x 35.6

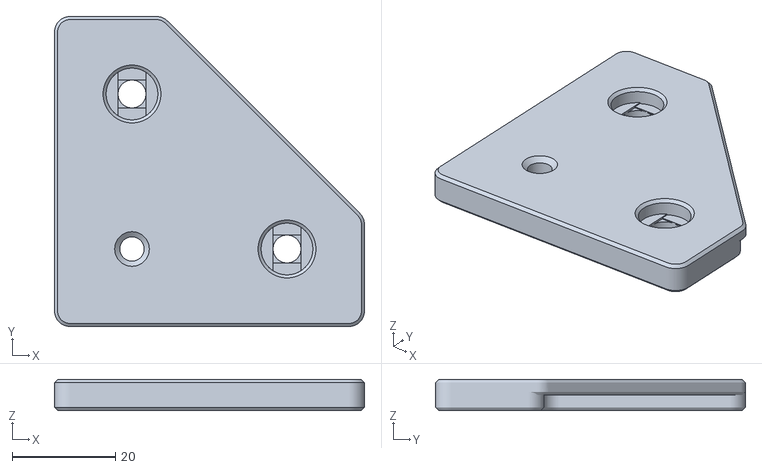
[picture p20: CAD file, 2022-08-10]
beta releases/beta 3/printed parts/panels/bottom panel mount.stl
60.0 x 60.0 x 6.00

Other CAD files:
beta releases/beta 3/printed parts/toolhead/LGX lite dragchain mount.stl
beta releases/beta 2/printed parts/electronics/PSU mount cover.stl
beta releases/beta 2/printed parts/misc/cable raceway cover.stl
beta releases/beta 2/printed parts/motion/bed rail mount front left.stl
beta releases/beta 2/printed parts/electronics/PSU mounting bracket.stl
beta releases/beta 2/printed parts/electronics/SSR cover.stl
beta releases/beta 2/printed parts/electronics/SSR enclosure.stl
beta releases/beta 2/printed parts/electronics/electronics enclosure.stl
beta releases/beta 2/printed parts/electronics/electronics lid.stl
beta releases/beta 2/printed parts/electronics/stepper inlet 2X.stl
beta releases/beta 2/printed parts/electronics/toolhead inlet bottom.stl
beta releases/beta 2/printed parts/electronics/toolhead inlet top.stl
beta releases/beta 2/printed parts/misc/air filter body 2X.stl
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

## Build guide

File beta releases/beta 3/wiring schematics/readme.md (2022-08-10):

these schematics are slightly out of date, as the connector type has changed, but is still a good reference point for wiring the printer

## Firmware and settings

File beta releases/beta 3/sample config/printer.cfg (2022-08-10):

# This file contains a default setup for the melty printer using a BTT octopus PRO with TMC5160HV driver in the first 4 slots and TMC2209 drivers in the remaining 4 slots.
# To use this config, the firmware should be compiled for the STM32F446 with a "32KiB bootloader"
# Enable "extra low-level configuration options" and select the "12MHz crystal" as clock reference

# after running "make", copy the generated "klipper/out/klipper.bin" file to a
# file named "firmware.bin" on an SD card and then restart the OctoPus with that SD card.

# See docs/Config_Reference.md for a description of parameters.

# this config is untested, use with caution.


[printer]
kinematics: cartesian
max_velocity: 1000
max_accel: 20000
max_accel_to_decel: 20000
max_z_velocity: 50
max_z_accel: 2000
square_corner_velocity: 20

########################################
# TMC5160 configuration
#these are configured for the first 4 slots on the board
########################################

[tmc5160 stepper_x]
cs_pin: PC4
run_current: 1.2
interpolate: False
stealthchop_threshold: 0
spi_software_mosi_pin: PA7
spi_software_miso_pin: PA6
spi_software_sclk_pin: PA5
diag0_pin: !PG6
driver_SGT: 1                   #tune this

[tmc5160 stepper_x1]
cs_pin: PD11
run_current: 1.2
interpolate: False
stealthchop_threshold: 0
spi_software_mosi_pin: PA7
spi_software_miso_pin: PA6
spi_software_sclk_pin: PA5
diag0_pin: !PG9
driver_SGT: 1                   #tune this

[tmc5160 stepper_y]
cs_pin: PC6
run_current: 1.2
interpolate: False
stealthchop_threshold: 0
spi_software_mosi_pin: PA7
spi_software_miso_pin: PA6
spi_software_sclk_pin: PA5
diag0_pin: !PG10
driver_SGT: 1                   #tune this

[tmc5160 stepper_y1]
cs_pin: PC7
run_current: 1.2
interpolate: False
stealthchop_threshold: 0
spi_software_mosi_pin: PA7
spi_software_miso_pin: PA6
spi_software_sclk_pin: PA5
diag0_pin: !PG11
driver_SGT: 1                   #tune this

########################################
# TMC2209 configuration
# these are configured for the last 4 stepper slots
########################################

[tmc2209 stepper_z]
uart_pin: PF2
run_current: 0.7
interpolate: False
stealthchop_threshold: 0

[tmc2209 stepper_z1]
uart_pin: PE4
run_current: 0.7
interpolate: False
stealthchop_threshold: 0

[tmc2209 stepper_z2]
uart_pin: PE1
run_current: 0.7
interpolate: False
stealthchop_threshold: 0

[tmc2209 extruder]
uart_pin: PD3
run_current: 0.6
interpolate: False
stealthchop_threshold: 0

#[tmc5160 extruder] #running 48v for the extruder
#cs_pin: PD3
#run_current: 0.7
#interpolate: False
#stealthchop_threshold: 0
#spi_software_mosi_pin: PA7
#spi_software_miso_pin: PA6
#spi_software_sclk_pin: PA5

########################################
# TMC2209 configuration
# these are configured for the first 4 stepper slots (used when not running 48V)
########################################

#[tmc2209 stepper_x]
#uart_pin: PC4
#run_current: 1.2
#interpolate: False
#stealthchop_threshold: 0
#diag_pin: PG6
#driver_SGTHRS: 90                   #tune this

#[tmc2209 stepper_x1]
#uart_pin: PD11
#run_current: 1.2
#interpolate: False
#stealthchop_threshold: 0
#diag_pin: PG9
#driver_SGTHRS: 90                   #tune this

#[tmc2209 stepper_y]
#uart_pin: PC6
#run_current: 1.2
#interpolate: False
#stealthchop_threshold: 0
#diag_pin: PG10
#driver_SGTHRS: 90                   #tune this

#[tmc2209 stepper_y1]
#uart_pin: PC7
#run_current: 1.2
#interpolate: False
#stealthchop_threshold: 0
#diag_pin: PG11
#driver_SGTHRS: 90                   #tune this

########################################
# stepper configuration
########################################


[stepper_x]
step_pin: PF13
dir_pin: !PF12
enable_pin: !PF14
microsteps: 16
rotation_distance: 40
full_steps_per_rotation: 200
endstop_pin: tmc5160_stepper_x:virtual_endstop
position_endstop: 256
position_max: 256
homing_speed: 60
homing_positive_dir: True
homing_retract_dist: 0

[stepper_x1]
step_pin: PG0
dir_pin: PG1
enable_pin: !PF15
microsteps: 16
rotation_distance: 40
endstop_pin: tmc5160_stepper_x1:virtual_endstop 
full_steps_per_rotation: 200

[stepper_y]
step_pin: PF11
dir_pin: PG3
enable_pin: !PG5
microsteps: 16
rotation_distance: 40
full_steps_per_rotation: 200
endstop_pin: tmc5160_stepper_y:virtual_endstop 
position_endstop: 273
position_max: 273
homing_speed: 60
homing_positive_dir: True
homing_retract_dist: 0

[stepper_y1]
step_pin: PG4
dir_pin: PC1
enable_pin: !PA0
microsteps: 16
rotation_distance: 40
full_steps_per_rotation: 200
endstop_pin: tmc5160_stepper_y1:virtual_endstop 


[stepper_z]
step_pin: PF9
dir_pin: PF10
enable_pin: !PG2
microsteps: 32
rotation_distance: 8
full_steps_per_rotation: 200
endstop_pin: probe:z_virtual_endstop
homing_speed: 50
position_max: 290
position_min: -40.0

[stepper_z1]
step_pin: PC13
dir_pin: !PF0
enable_pin: !PF1
microsteps: 32
rotation_distance: 8
full_steps_per_rotation: 200

[stepper_z2]
step_pin: PE2
dir_pin: !PE3
enable_pin: !PD4
microsteps: 32
rotation_distance: 8
full_steps_per_rotation: 200

[safe_z_home]
home_xy_position: 125, 132
speed: 1000
z_hop: 30
z_hop_speed: 50.0

[probe]
pin: PC5
x_offset: 0.0
y_offset: 30.0   
#z_offset: 0.0
speed: 50

[extruder]
step_pin: PE6   
dir_pin: PA14
enable_pin: !PE0
microsteps: 16
full_steps_per_rotation: 200
#rotation_distance: 7.780624   #LGX. fine tune for your specific setup
#rotation_distance: 5.61   #LGX lite. fine tune for your specific setup
nozzle_diameter: 0.400
filament_diameter: 1.750
heater_pin: PA2
sensor_pin: PF3
#sensor_type: ATC Semitec 104NT-4-R025H42G     #set your thermistor type used
#control: pid          #tune your PID before printing
pid_Kp: 22.2
pid_Ki: 1.08
pid_Kd: 114
min_temp: -200
max_temp: 330
min_extrude_temp: 0
max_extrude_cross_section: 9999999999
max_extrude_only_distance: 9999999999

########################################
# misc stuff
########################################

[idle_timeout]
timeout: 86400

[heater_bed]
heater_pin: PA3
sensor_pin: PF6
#sensor_type: Generic 3950     #set your thermistor type used
#control: pid     #tune your PID before printing
pid_Kp: 22.2
pid_Ki: 1.08
pid_Kd: 114
min_temp: 0
max_temp: 140
max_power: 0.7

[gcode_arcs]
resolution: 0.1

[mcu]
#serial: /dev/serial0     #set this to your used communication. this is set up for UART
baud: 250000
restart_method: command

[temperature_sensor raspberry_pi]
sensor_type: temperature_host
min_temp: 0
max_temp: 80

[temperature_sensor mcu_temp]
sensor_type: temperature_mcu
min_temp: 0
max_temp: 80

[temperature_sensor stepper]
sensor_type: Generic 3950
sensor_pin: PF5
min_temp: 0
max_temp: 130

[bed_mesh] #if your bed is flat enough, you might be able to get away without a bed mesh 
speed: 1000
horizontal_move_z: 3
mesh_min: 20, 35
mesh_max: 230, 230
probe_count: 3,3
mesh_pps: 4,4
algorithm: lagrange
move_check_distance: 5
split_delta_z: 0.025

[z_tilt]
z_positions: 
    -44,43
    132,306
    324,43
points: 
    35,25
    132,205 
    230,25
speed: 1000
horizontal_move_z: 15
retries: 10
retry_tolerance: 0.01

[fan]
pin: PD12

[output_pin LED]
pin: PD14
pwm: True 
cycle_time: 0.010

[heater_fan extruder]
pin: PE5 
fan_speed: 1.0
heater_temp: 50.0
heater: extruder

[controller_fan electronics]
pin: PA8
idle_timeout: 120

[heater_fan bed]
pin: PD13 
fan_speed: 1.0
heater_temp: 60.0
heater: heater_bed

[pause_resume]

[virtual_sdcard]
path: ~/gcode_files

[display_status]

[force_move]
enable_force_move: True

[input_shaper] # you need to tune these for your specific printer as they will be different
shaper_freq_x: 67.4
shaper_type_x: mzv
damping_ratio_x: 0.04
shaper_freq_y: 69.4
shaper_type_y: mzv
damping_ratio_y: 0.04

[mcu rpi]
serial: /tmp/klipper_host_mcu

[adxl345]
cs_pin: rpi:None

[resonance_tester]
accel_chip: adxl345
probe_points:
    125, 132, 20 

[skew_correction]

#######################################
#macros
#######################################

[gcode_macro PAUSE]
rename_existing: BASE_PAUSE
#default_parameter_E: 1.7
gcode:
    {% set x_park = printer.toolhead.axis_maximum.x|float - 5.0 %}
    {% set y_park = printer.toolhead.axis_maximum.y|float - 5.0 %}
    {% set max_z = printer.toolhead.axis_maximum.z|float %}
    {% set act_z = printer.toolhead.position.z|float %}
    {% if act_z < (max_z - 2.0) %}
        {% set z_safe = 2.0 %}
    {% else %}
        {% set z_safe = max_z - act_z %}
    {% endif %}
    SAVE_GCODE_STATE NAME=PAUSE_state
    BASE_PAUSE
    G91
    G1 E-1 F2100
    G1 Z{z_safe}
    G90
    G1 X{x_park} Y{y_park} F6000
    G91

[gcode_macro RESUME]
rename_existing: BASE_RESUME
#default_parameter_E: 1.7
gcode:
  G91
  G1 E1 F2100
  RESTORE_GCODE_STATE NAME=PAUSE_state
  BASE_RESUME
  
[gcode_macro CANCEL_PRINT]
description: Cancel the actual running print
rename_existing: CANCEL_PRINT_BASE
gcode:
  TURN_OFF_HEATERS
  CANCEL_PRINT_BASE
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

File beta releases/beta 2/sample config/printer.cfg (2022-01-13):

# This file contains a default setup for the melty printer using a BTT octopus PRO with TMC5160HV driver in the first 4 slots and TMC2209 drivers in the remaining 4 slots.
# To use this config, the firmware should be compiled for the STM32F446 with a "32KiB bootloader"
# Enable "extra low-level configuration options" and select the "12MHz crystal" as clock reference

# after running "make", copy the generated "klipper/out/klipper.bin" file to a
# file named "firmware.bin" on an SD card and then restart the OctoPus with that SD card.

# See docs/Config_Reference.md for a description of parameters.

# this config is untested, use with caution.

[include macros.cfg] #the seperate file for macro commands. place the file in the same directory as this file

[printer]
kinematics: cartesian
max_velocity: 500
max_accel: 5000
max_z_velocity: 10
max_z_accel: 500
square_corner_velocity: 5.0

########################################
# TMC5160 configuration
########################################

[tmc5160 stepper_x]
cs_pin: PC4
run_current: 1.500
interpolate: False
stealthchop_threshold: 0
spi_software_mosi_pin: PA7
spi_software_miso_pin: PA6
spi_software_sclk_pin: PA5

[tmc5160 stepper_x1]
cs_pin: PD11
run_current: 1.500
interpolate: False
stealthchop_threshold: 0
spi_software_mosi_pin: PA7
spi_software_miso_pin: PA6
spi_software_sclk_pin: PA5

[tmc5160 stepper_y]
cs_pin: PC6
run_current: 1.500
interpolate: False
stealthchop_threshold: 0
spi_software_mosi_pin: PA7
spi_software_miso_pin: PA6
spi_software_sclk_pin: PA5

[tmc5160 stepper_y1]
cs_pin: PC7
run_current: 1.500
interpolate: False
stealthchop_threshold: 0
spi_software_mosi_pin: PA7
spi_software_miso_pin: PA6
spi_software_sclk_pin: PA5

########################################
# TMC2209 configuration
########################################

[tmc2209 stepper_z]
uart_pin: PF2
run_current: 0.700
interpolate: False
stealthchop_threshold: 0

[tmc2209 stepper_z1]
uart_pin: PE4
run_current: 0.700
interpolate: False
stealthchop_threshold: 0

[tmc2209 stepper_z2]
uart_pin: PE1
run_current: 0.700
interpolate: False
stealthchop_threshold: 0

[tmc2209 extruder]
uart_pin: PD3
run_current: 0.500
interpolate: False
stealthchop_threshold: 0

########################################
# stepper configuration
########################################


[stepper_x]
step_pin: PF13
dir_pin: PF12
enable_pin: !PF14
microsteps: 32
rotation_distance: 40
full_steps_per_rotation: 200
endstop_pin: PG12
position_endstop: 261
position_max: 261
homing_speed: 30
second_homing_speed: 20

[stepper_x1]
step_pin: PG0
dir_pin: !PG1
enable_pin: !PF15
microsteps: 32
rotation_distance: 40
full_steps_per_rotation: 200

[stepper_y]
step_pin: PF11
dir_pin: PG3
enable_pin: PG6
microsteps: 32
rotation_distance: 40
full_steps_per_rotation: 200
endstop_pin: PG10
position_endstop: 271
position_max: 271
homing_speed: 30
second_homing_speed: 1

[stepper_y1]
step_pin: PG4
dir_pin: PC1
enable_pin: !PA0
microsteps: 32
rotation_distance: 40
full_steps_per_rotation: 200


[stepper_z]
step_pin: PF9
dir_pin: PF10
enable_pin: !PG2
microsteps: 32
rotation_distance: 8
full_steps_per_rotation: 200
endstop_pin: probe:z_virtual_endstop
homing_speed: 30
position_max: 290
position_min: -3.0

[stepper_z1]
step_pin: PC13
dir_pin: PF0
enable_pin: !PF1
microsteps: 32
rotation_distance: 8
full_steps_per_rotation: 200

[stepper_z2]
step_pin: PE2
dir_pin: PE3
enable_pin: !PD4
microsteps: 32
rotation_distance: 8
full_steps_per_rotation: 200

[homing_override]
axes: z
set_position_z: 0
gcode:
    G90
    G0 Z5 F1800
    G28 X0 Y0 F1800
    G0 X138 Y132 F18000
    G28 Z0 F1800
    G0 Z5 F1800

[probe]
pin: ^PG13
x_offset: 0.0
y_offset: 30.0
z_offset: 0.0
speed: 35

[extruder]
step_pin: PE6   
dir_pin: PA14
enable_pin: !PE0
microsteps: 16
rotation_distance: 7.780624
nozzle_diameter: 0.400
filament_diameter: 1.750
heater_pin: PA2
sensor_pin: PF3
sensor_type: EPCOS 100K B57560G104F
control: pid
pid_Kp: 22.2
pid_Ki: 1.08
pid_Kd: 114
min_temp: 0
max_temp: 290
max_extrude_cross_section: 9999

[fan]
pin: PD12

[heater_fan extruder]
pin: PE5 
fan_speed: 1.0
heater_temp: 50.0
heater: extruder

########################################
# misc stuff
########################################

[idle_timeout]
timeout: 7200

[heater_bed]
heater_pin: PA3
sensor_pin: PF4
sensor_type: EPCOS 100K B57560G104F
control: pid
pid_Kp: 22.2
pid_Ki: 1.08
pid_Kd: 114
min_temp: 0
max_temp: 130

[gcode_arcs]
resolution: 0.1

[mcu]
serial: /dev/serial/by-id/usb-Klipper_Klipper_firmware_12345-if00 #change this, this might be different on your printer
restart_method: command

[temperature_sensor raspberry_pi]
sensor_type: temperature_host
min_temp: 0
max_temp: 80

[temperature_sensor mcu_temp]
sensor_type: temperature_mcu
min_temp: 0
max_temp: 80

[bed_mesh] #if your bed is flat enough, you might be able to get away without a bed mesh 
speed: 500
horizontal_move_z: 5
mesh_min: 10, 10
mesh_max: 240, 240
probe_count: 5,5
mesh_pps: 2,2
algorithm: lagrange

[z_tilt]
z_positions: 
    -44,-42
    132,328
    324,-42
points: 
    10,15
    132,215 
    245,15
speed: 500
horizontal_move_z: 15
retries: 10
retry_tolerance: 0.0025

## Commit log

2022-01-13 beta 2
    [1515 rail tool 4X.3mf, 3030 rail tool 4X.3mf, BOM.xlsx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]
2022-08-10 beta 3
    [BOM.xlsx, CF tube insert.stl, LGX drag chain mount.stl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]
2022-08-11 fixed offset motor in cad
